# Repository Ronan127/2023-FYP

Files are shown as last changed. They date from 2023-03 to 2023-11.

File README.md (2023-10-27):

# 2023-FYP

Using this repository:

This repository contains the full project folder for my final year project. If you are continuing this project, I recommend cloning this repository or downloading the MATLAB/ and vscode/ folders.

Using the maths model:

The maths model was developed in MATLAB and can be found in MATLAB/v2/.  The Calculations.mlx contains the code I used to produce the plots in the report. The first section loads the stored sets of equations. These equations are produced by the scripts SetCoreEquations.m and SetDesignParameters.m.
To model devices other than the one I used in this project, edit SetDesignParameters.m with your device's parameters and run it.

The next section in Calculations.mlx builds a set of equations from the core equations, the design parameters, the boundary conditions as described in the report, and the position of the device. The equations are fed to mysolver(), and the resulting solution contains T_z, the motor torque required to cause motion.
The solutions are used to create a visualisation of the device, which can be useful to ensure that all the angles lie in the correct quadrants and that the tail is contacting the correct steps. These steps are repeated for each stage of motion.

Next, the model is used to find solutions for a range of positions across a stage of motion. This is how I produced the torque-angle plot in the report. To do this, it first attempts to solve an incomplete set of equations that does not contain the position. The solver will find solutions to what it can, saving time in future steps.
Then, looping through all the positions you want to solve for, the positions are added to the remaining equations and solved. This takes some time, despite making use of parallelization.

Next, the model is used to determine how changing the gear ratios affects the required torque and friction. To do this, it first creates a new set of design parameters that do not define the gear ratio, then the solver loops through different values for the number of teeth on the planet gear. The highest torque and friction required are in Stage 4 and are not at a set angle, so the solver attempts several angles and finds the one that produces the highest torque.
This example can be expanded to explore any design parameter; just make sure to check whether increasing the size of the tail or LIMs changes which steps the LIMS make contact with.

The one major weakness of mysolver() is that it cannot identify whether the equations are overdefined. If you have x == 2 and x == 3, it will just pick the first one, so bear that in mind when using this tool.

Using the converter:

Drake does not support Windows, so Linux or OSX is needed. I set up the conversion pipeline and simulation in Ubuntu using the Windows Subsystem for Linux. I recommend installing Visual Studio code for WSL for these next steps.

This stage primarily uses onshape-to-robot, which can be found at https://github.com/Rhoban/onshape-to-robot
They have a well-documented program, however if you just want to use my scripts, this is what you would need to do:
1. Clone or download vscode/ into your Linux installation
2. Create a Python virtual environment in this folder
3. Run pip install -r requirements.txt
4. Get an Onshape account
5. Get an access key and secret key from https://dev-portal.onshape.com/keys
6. Edit convert.sh with your keys (Note that this is not secure, and there are better ways of doing it. Do not publish this file while it has your keys in it. I have deactivated mine.)
7. Now you need a file to convert. onshape-to-robot has a list of requirements for the onshape file. I recommend you ensure whatever device you build conforms to their guidelines. My design, https://cad.onshape.com/documents/9f7ac96b4bf1f871a2a6bcc9/, can be used as a guideline for naming conventions and subassembly grouping. My code specifically looks for joints named dof_motor_a and dof_motor_b_inv, and links named Tail, Wheel, and Frame.
8. Once you have a device ready, create a new folder containing a file named config.json, with the contents:
   {
    "documentId": "Your document ID",
    "outputFormat": "sdf"
   }
   "Your document ID" is the first set of hex codes in the device's URL. For my design, it is 9f7ac96b4bf1f871a2a6bcc9.
9. Then run "convert.sh yourFolder" where yourFolder is the name of the folder you created in step 8.
10. The folder should now populate with a .sdf file and all of the object files.

Using the simulator:

To run the simulation, run simulation.py. This will open a meshcat instance, which can be opened at http://localhost:7000/. The code here is primarily based on the tutorial: https://deepnote.com/workspace/Drake-0b3b2c53-a7ad-441b-80f8-bf8350752305/project/Tutorials-2b4fc509-aef2-417d-a40d-6071dfed9199/notebook/authoring_multibody_simulat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
simulation.py has many private defines that can be edited, such as the .sdf file location, stair sizes, and motor properties.
If the simulator ever pulls an exception, try decreasing the time step or increasing the no-load speed; it is likely because the feedback from the motor equation is too sharp.

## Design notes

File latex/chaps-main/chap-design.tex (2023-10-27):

\chapter{Design}

In order to validate the model, a device must be designed, built and tested. 

\section{Selection of design parameters}
There are many parameters to consider when designing LIMs, such as gear ratios, lengths, and wheel size. Optimising the design is beyond the scope of this project, but the device does need to work to the extent that it can be used to validate the model. Initially, this project intended to use the early versions of the model to inform the design process. However, as the model was not yet validated, significantly changing key parameters could easily result in a device that is unable to climb stairs at all. Previous projects were able to show inconsistent success. Of the previous projects, Powrie's design was the latest and most informed, and is used as a starting point for this project. Powrie's report specifies the dimensions and gear ratios for the LIMs used in this project.\\

\section{Body design}
The body of the device is the central part that contains the motors and any peripheral devices.
Powrie's design for the body includes a camera, batteries, and extra gearing to increase the torque of his motor. These components are superfluous for the objectives of this project, and are not included in the design. Additionally, the body in Powrie's design protrudes forward significantly beyond the axle of the LIMs. This is done to allow for gearing of the axial motors used in the design, but previous students have found that this protrusion causes the body to collide with the step when climbing, which can result in failure to climb the step. This project uses DC motors with worm gearbox outputs, allowing the motor to be placed at a right angle to the axis. This eliminates the need for significant forward protrusion or additional gearing, and simplifies the construction process. Figures \ref{fig:Powrie-internals} and \ref{fig:internals} shows the body of Powrie's design and this project's design respectively.
\begin{figure}
	\centering
	\begin{subfigure}{.5\textwidth}
		\centering
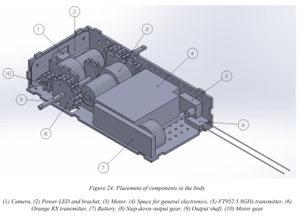
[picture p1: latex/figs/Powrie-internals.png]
		
		\caption{Powrie's design of the body.}
		\label{fig:Powrie-internals}
	\end{subfigure}%
	\begin{subfigure}{.5\textwidth}
		\centering
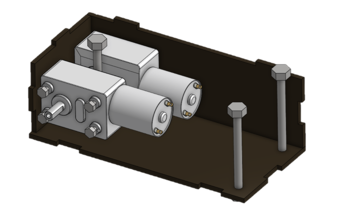
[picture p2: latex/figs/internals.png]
		
		\caption{This project's design of the body.}
		\label{fig:internals}
	\end{subfigure}
	\caption{Body design comparison.}
	\label{fig:bodies}
\end{figure}

\section{Motor selection}
Brushed DC motors often include a gearbox to increase the torque of the output at the cost of speed. For this design, the output shaft must be at a right angle to the motor, which is typically done with a worm gearbox. The most readily available motors that meet these requirements are the JGY-370 12V DC worm gear motors, which come with a range of gear ratios. Initially, the 40 RPM model was selected as it provides similar torque to the EGB-380S with added gearing that Powrie used, however initial tests indicated that additional torque was needed for consistent climbing, so the 6 RPM model was used instead.\\
Additionally, these motors have a self-locking gearbox, which improves the controllability of the device, as shutting off the motors will cause the gearbox to lock and the device to stop moving, rather than allowing the device to fall backwards down the steps.

\section{Control circuits and code}
In order to validate the model, the torque of the motors must be variable and reversible. This project uses a L298n H-bridge controlled by an STM32-F303RE Nucleo board to drive the motors. Two potentiometer sliders are used to control the torque of the two motors independently. The sliders are set up as voltage dividers and connected to the ADC channels of the STM32 microcontroller. The microcontroller sends a direction and PWM signal for each motor to the L298n H-bridge, which controls the motor using PWM. The circuit diagram for this set-up is shown in Figure \ref{fig:circuit-diagram}.

\begin{figure}[!h]
	\centering
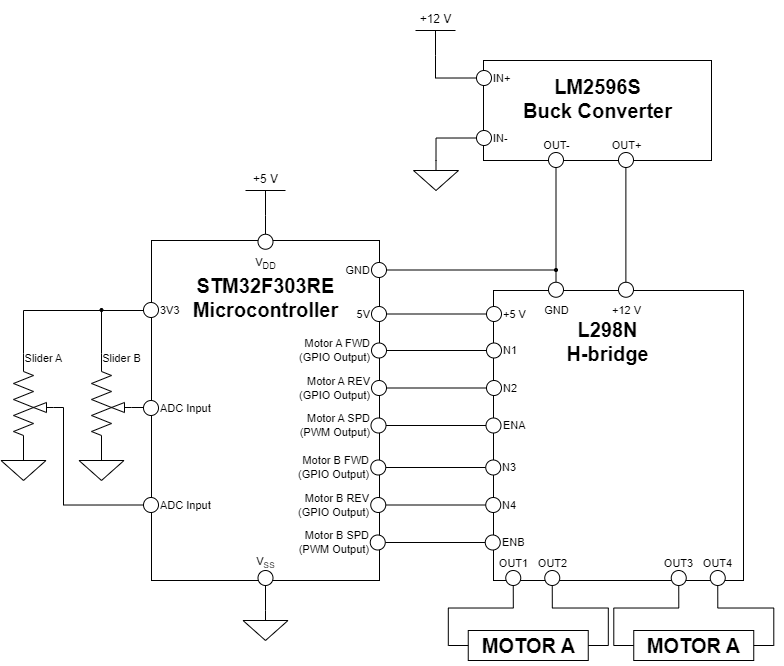
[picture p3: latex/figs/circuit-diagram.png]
	
	\caption{Control system circuit diagram.}
	\label{fig:circuit-diagram}
\end{figure}

The microcontroller is programmed to power off the motors when the sliders are centred, move the motors forward when the sliders are pushed forward, and move the motors in reverse when the sliders are pulled back. The PWM duty cycle is scaled such that when the ADC values are in the centre 20\% of their range, the PWM duty cycle is set to 0\%. When the ADC values are within the top or bottom 5\% of their range, the duty cycle is 100\%. The flow diagram for this code is shown in Figure \ref{fig:controller-flowchart}.

\begin{figure}[!h]
	\centering
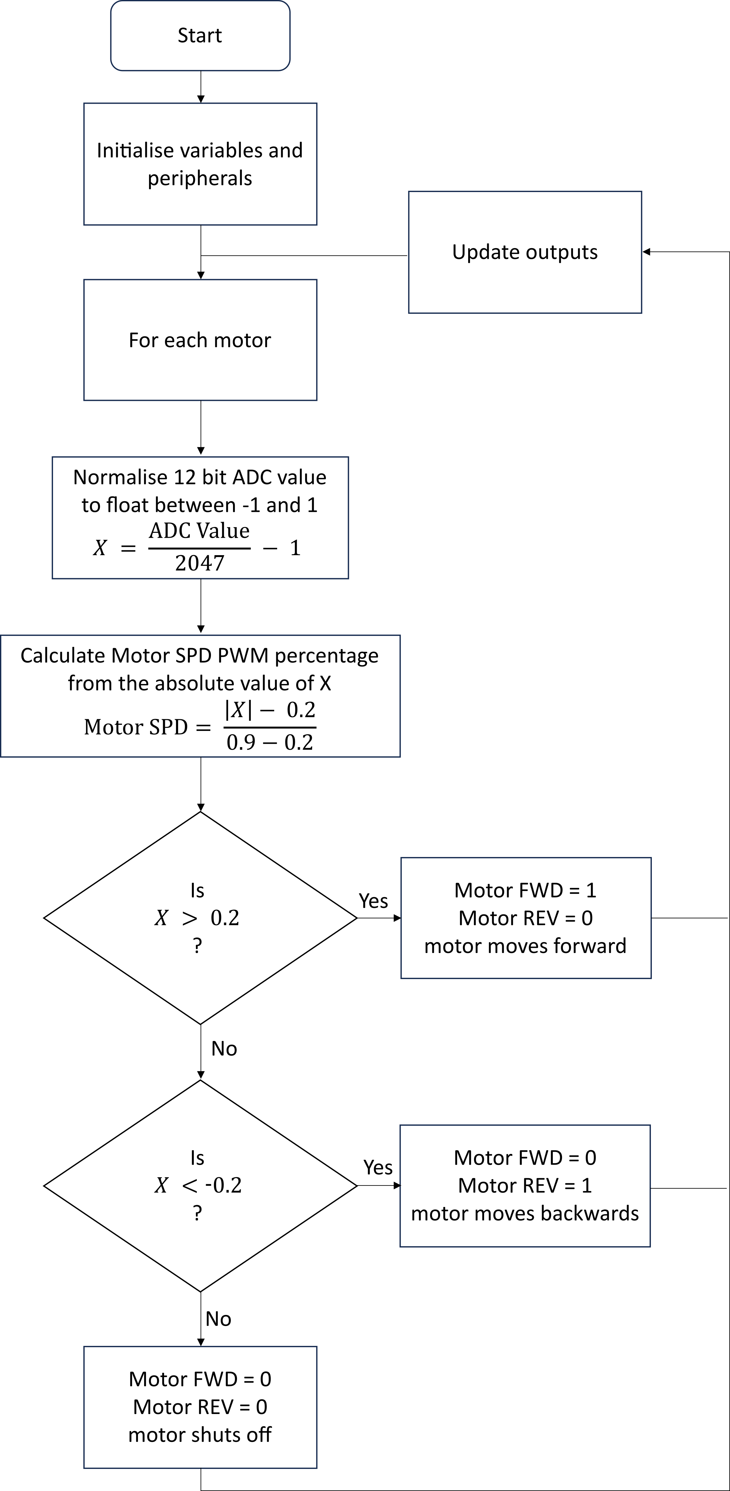
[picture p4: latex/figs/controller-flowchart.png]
	
	\caption{Microcontroller code flowchart.}
	\label{fig:controller-flowchart}
\end{figure}

Initial tests showed that PWM duty cycle is not proportional to torque output on the motors. Instead, even at low duty cycles, the motors can lift a large load, they just do so slowly. This is likely because the self-locking gearbox prevents the axle from ever falling backwards. Consider a DC motor lifting a lever as seen in Figure \ref{fig:lever}. 

\begin{wrapfigure}{r}{0.35\textwidth}
	\centering
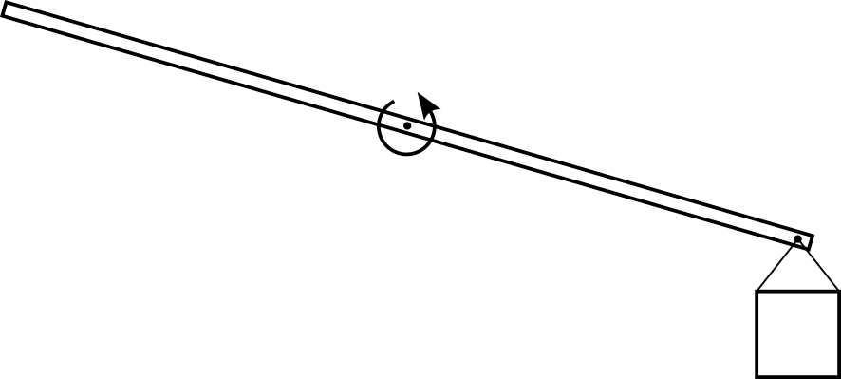
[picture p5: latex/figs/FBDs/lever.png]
	
	\caption{Lever example.}
	\label{fig:lever}
\end{wrapfigure}

Typically, when the PWM signal is on, the motor outputs full torque and moves forward, then when the PWM signal is off the motor outputs no torque and falls backwards. The PWM frequency is typically high enough that the human eye sees this as a smooth motion. However, because of the self-locking gearbox, the axle will lock when the PWM signal is off rather than moving backwards, resulting in an overall forward motion even at low duty cycles. This is quite useful for controlling the motors as the speed of the motors is proportional to the PWM duty cycle regardless of the load it must lift.\\

However, for the validation of the model, the motor torque should be variable and measurable. Brushed DC motor torque is proportional to the current running through it, and the current reduces as the speed of the motor increases. The speed of the motor is also proportional to the terminal voltage. The approximate characteristics of a DC motor are given in Figure \ref{fig:torque-speed}. 
\begin{figure}[!h]
	\centering
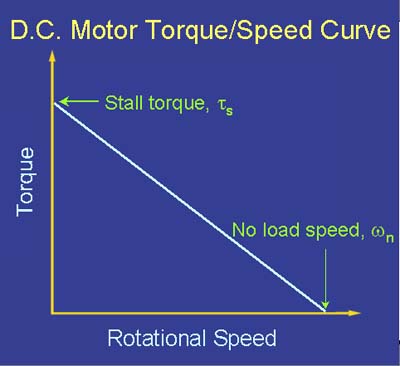
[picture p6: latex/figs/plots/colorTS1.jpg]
	
	\caption{Torque speed plot of a typical DC motor \citep{Page-1999}.}
	\label{fig:torque-speed}
\end{figure}

\noindent The equation describing the torque of a DC motor in relation to motor voltage and speed is then,
\begin{equation}
	T = T_\mathrm{Rated-stall}(\frac{V_\mathrm{Terminal}}{V_\mathrm{Rated}}-\frac{\omega}{\omega_\mathrm{Rated-no-load}})
\end{equation}
where $T$ is the output torque, $T_\mathrm{Rated-stall}$ is the stalling torque at the rated voltage, $V_\mathrm{Terminal}$ is the supply voltage across the motor terminals, $V_\mathrm{Rated}$ is the motor's rated supply voltage, $\omega$ is the rotational speed of the output shaft, and $\omega_\mathrm{Rated-no-load}$ is the speed of the output shaft when no load is placed on it at the rated voltage.\\

\noindent To solve for the stalling torque, $\omega$ is set to $0$. This gives the relation,
\begin{equation}
	T_\mathrm{Stall} = T_\mathrm{Rated-stall}\frac{V_\mathrm{Terminal}}{V_\mathrm{Rated}}
\end{equation}
%??? Move to literature review?
In order to vary the stall torque of the device, the terminal voltage must be varied. For this purpose, an LM2596S buck converter is used to vary the supply voltage.

\section{Construction and testing}\label{sec:construction}

\begin{wrapfigure}{r}{0.35\textwidth}
	\centering
	
	\caption{Built device.}
	\label{fig:device}
\end{wrapfigure}

To build the device, the parts were laser cut from Medium Density Fibreboard (MDF) and Acrylic. The outer surface of wheels is coated with Patex, a rubbery adhesive which is left to dry, increasing the grip of the wheels. The assembly is relatively straightforward, however it was found that the laser cut gears did not mesh well, causing them to get stuck. To address this, the teeth of the gears were filed down until they could mesh easily. This has the disadvantage of increasing kickback on the gears. However, this has little impact on performance as for all stages of motion, the gears are engaged in one direction only. The device is shown in Figure \ref{fig:device}.\\

Initial tests show that the device is capable of climbing up two steps sequentially, which is more than any previous project achieved. This relative success can be attributed to the shorter forward protrusion of the body and possibly a higher grip on the surface of the wheels. However, the device struggled to climb a third step, this is because climbing the third step involves Stage 4 motion, which requires significantly higher torque than the previous stages. To address this, the body of the device was rebuilt using a JGY-370 gearbox motor which is geared for a higher torque. \\
After this change, the device was able to consistently climb many sequential steps, and the lower speed due to the higher gear ratio made the device easier to control during the climbing motion. Figure \ref{fig:device-climbing} shows the device climbing a flight of stairs. Initial tests also show that by applying a forward torque to one LIM and a reverse torque to the other, the device is capable of turning on the spot. However this motion is inconsistent as the LIMs can start to lift, at which point the turning stops.
\begin{figure}[!ht]
	\centering
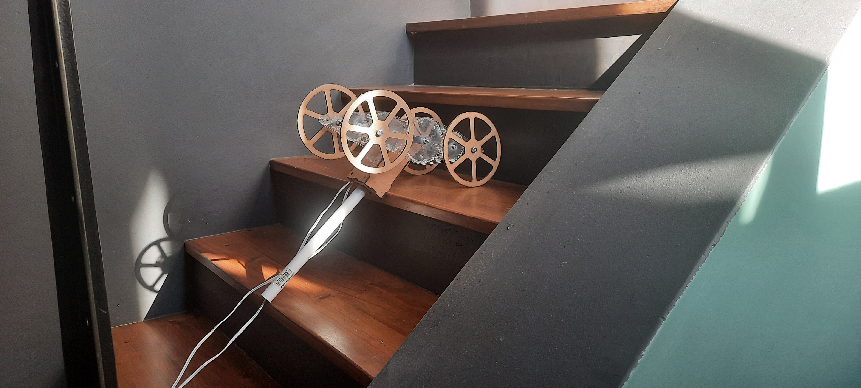
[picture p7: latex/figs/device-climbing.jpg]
	
	\caption{Device climbing stairs.}
	\label{fig:device-climbing}
\end{figure}
%When the motor is turning it also acts as a generator, and produces a voltage known as back emf which is proportional to the speed of the motor. 
%\begin{equation}
%	E_b \propto \omega
%\end{equation}
%Where $E_b$ is the back emf and $\omega$ is the speed of the motor.
%
%The approximate circuit diagram of a DC motor is shown in figure ???. The current running through the motor is proportional to the difference between the supply voltage and the back emf.
%\begin{subequations}
%	\begin{align}
%	I &= \frac{V-E_b}{R_a
%	I &\propto V-E_b
%	\end{align}
%\end{subequations}

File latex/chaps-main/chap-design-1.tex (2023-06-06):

\chapter{Design- 1st iteration}

Starting with Powrie's device as it is the most developed of the previous projects.\\
Attempted to use mathematical model to identify potential improvements, however I struggled to get objective improvements, increasing one parameter often may improve the ability to flip but hinder the ability to climb overall, and removing material should only be done if it has minimal effect on structure strength, something that would take much time to determine (possibly with FEM?). Such optimisations are beyond the scope of the project, I'm not trying to create a perfectly optimised device, I'm trying to create a working device so I can describe its function. Powrie’s device is working to some extent, so the first design iteration should deviate minimally from his design.\\
Powrie's design for the LIMs is copied as accurately as possible, could possibly even use his laser cutting templates to manufacture. Fortunately he provides a detailed builder's guide, allowing me to design and build ASAP so I can focus on the math model. The robot body is changed significantly. Powrie uses external gears on an already geared motor, this is unnecessary, as geared motors come in a variety of ratios. I use a JGY-370 motor, as I believe the worm gearbox is well suited to this purpose, it allows me to make a thinner body that doesn't protrude as far forward beyond the axle. The tail is designed based on Powrie’s concepts. The motors selected produce more torque than the ones Powrie selected, even with his additional gearing, so they should be up to the task. Later iterations could combine the worm gearbox with even more powerful brushless motors.

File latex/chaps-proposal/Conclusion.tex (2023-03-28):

\chapter{Conclusions}
%In conclusion, sound localisation is a promising technology that could be used in more applications if it were more precise. The proposed project will design and build a sound localisation device, and investigate methods to improve its performance. The project activities have been outlined and planned, risks have been assessed, and an expected budget of R221725 is presented.
USAR robots are a promising technology for disaster response. Reducing the cost of these robots will make them more accessible. The proposed project will provide a model to describe the kinematics of USAR robots that use LIMs for locomotion to reduce costs, and will produce a prototype of a USAR robot platform to show that the model is accurate. The result of these activities will be a validated model that can be used to inform future USAR designs using LIMs.\\

\noindent The project activities have been outlined and the project risks have been assessed and mitigated. The expected duration of the project is 8 months and the expected budget is R265 400.

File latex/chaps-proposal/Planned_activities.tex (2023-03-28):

\chapter{Planned Activities}

\section{Review Literature}
Study work by previous students on LIMed robots. Additionally, research existing solutions for USAR platforms and identify methods that are applicable to this project. 

\section{2D Simulation}
Perform a simple 2D simulation of a LIMed robot platform to gain a greater understanding of how it functions.

\section{Create Model}
Create a mathematical model to describe the kinematics of a LIMed robot platform. This will be presented in a way that describes how the degrees of freedom will move as a function of the platform's state and the torque applied to it.

\section{Compile Design Requirements}
Determine the requirements for the system, including functions that the platform must be able to perform and the cost of the platform. List these requirements in a way that they can be used to evaluate different concepts.

\section{Design Platform}
Compare concepts for a LIMed robot platform, then select the preferred concept based on its ability to meet the design requirements. Then create a detailed design of the robot platform.

\section{Simulate Platform}
Perform a mature simulation of the designed platform to ensure it will meet the requirements.

\section{Produce Prototype}
Construct a prototype of the robot platform. This will involve a combination of manufacture by the MMW, and assembly of the components.

\section{Validate Model}
Test that the model accurately describes the kinematics of a LIMed system through experimentation using the prototype.

\section{Finalise Report}
Document the entire project, including the process of creating a model, designing and production of the prototype, and experimentation. Comment on whether the model can be used to accurately describe the LIM system.\\\\

\noindent Please see Appendix A for the budget and time allocation of these activities.

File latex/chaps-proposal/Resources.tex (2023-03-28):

\chapter{Resource use and end of life strategy}

This project will build a prototype device that has a motor, a controller, wheels, and several custom parts such as gears and frames. A battery is unlikely to be included as it may be too expensive for a prototype build which can otherwise be wired to a power supply.
The prototype will likely benefit from having a low mass, so there is already an incentive to use materials sparingly. Before construction, the design will be simulated to ensure that it meets requirements; this will mitigate the chance that a second prototype will need to be built. Upon completion of the project, the prototype will be disassembled and the motor, controller, and wheels can be reused in future projects. The custom parts are specific to this design so will not be suitable for most reuse applications; they shall be recycled. If the materials are such that they cannot be recycled, then they shall be disposed of instead. These materials will be chemically inert (not hazardous).

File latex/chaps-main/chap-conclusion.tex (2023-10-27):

\chapter{Conclusions}

This report details the design, modelling, and model validation of a novel gearing system for robot locomotion. The advantage of this LIM gearing system is that it allows a device to roll forward or climb steps using a single actuator, reducing costs, while also being able to fit into low voids. The model produced by this report could be used to inform the design of future USAR robots. This project builds and improves upon previous work, and produces the first LIM robot capable of climbing steps consistently and sequentially. \\

To explore the motion of the LIMs, a preliminary two-dimensional simulation was performed, and the stair climbing motion of the device was categorised into six distinct stages. This project proposes a mathematical model to describe the motion a LIMed device, using the MATLAB symbolic toolbox. The maths model consists of a large set of simultaneous equations that are solved simultaneously, and this report presents an algorithm that uses the MATLAB functions to efficiently solve this large set of equations. Additionally, this project explores the use of Drake, a multi-body simulator, to model the device. \\

Both the maths model and simulation are validated against real world data. The validation showed that the torque required to climb stairs sequentially was 16.4\% higher than the maths model predicted, and 5.9\% higher than the simulation predicted. This report explores the reasons for this error, which are attributed to imperfect assumptions and calibration methods.\\

In conclusion, this project was successful in completing its objectives. Both the model and simulation have been validated and their error has been quantified, they can be used to inform future work on LIMed robots.

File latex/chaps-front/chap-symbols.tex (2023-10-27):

\chapter{List of symbols}
% Use stb-nomenclature + siunitx

\begin{Nomencl}[1cm]
\NomGroup{Constants}%-----------------------------------------------
    \item[$g = $] \qty{9.81}{m/s^2}
\NomGroup{Components}%-----------------------------------------------
	\item[1] LIM frame
	\item[2] Central or "sun" gear
	\item[3] Front idler gear
	\item[4] Rear idler gear
	\item[5] Front outer or "planet" gear
	\item[6] Rear outer or "planet" gear
	\item[7] Body of the device, including the motors and the tail
\NomGroup{Variables}%-----------------------------------------------
	\item[$I_n$]
	\UnitLine{Mass moment of inertia of component n, normal and relative to its relevant axis}{kg.m^2}
	\item[$M_{\mathrm{React}n}$]
	\UnitLine{Reaction moment that the ground or step exerts on wheel n}{N.m}
	\item[$m_n$]
	\UnitLine{Mass of component n}{kg}
	\item[$N$]
	\UnitLine{Number of the step on which the front wheel is placed}{~}
	\item[$N_2$]
	\UnitLine{Number of the step on which the tail makes contact}{~}
	\item[$N_{\mathrm{Planet}}$]
	\UnitLine{Number of teeth on the outer gear}{~}
	\item[$N_{\mathrm{Sun}}$]
	\UnitLine{Number of teeth on the central gear}{~}
	\item[$r_n$]
	\UnitLine{Radius of gear n}{rad/s^2}
	\item[$r_w$]
	\UnitLine{Radius of the wheels}{m}
	\item[$s_{7\mathrm{end}y}$]
	\UnitLine{3x1 Position vector of component the end of the tail}{m}
	\item[$T$]
	\UnitLine{Torque exerted by the motor of component 7 on component 2}{N.m}
	\item[$T_\mathrm{Rated-stall}$ ]
	\UnitLine{The motor stalling torque when the rated voltage is applied}{N.m}
	\item[$t$]
	\UnitLine{Time}{s}
	\item[$V_\mathrm{Rated}$ ]
	\UnitLine{The rated motor voltage}{V}
	\item[$V_\mathrm{Terminal}$ ]
	\UnitLine{The voltage across the motor terminals}{V}
	\item[$\theta_n$]
	\UnitLine{Clockwise angle of component n}{rad}
	\item[$\dot{\theta}_{\mathrm{Frame}}$]
	\UnitLine{Angular velocity of the frame}{rad/s}
	\item[$\dot{\theta}_{\mathrm{Planet}}$]         
	\UnitLine{Angular velocity of the outer gear and wheel}{rad/s}
	\item[$\dot{\theta}_{\mathrm{Sun}}$]
	\UnitLine{Angular velocity of the central gear}{rad/s}
	\item[$\dot{\theta_n}$]
	\UnitLine{Clockwise angular velocity of component n}{rad/s}
	\item[$\ddot{\theta_n}$]
	\UnitLine{Clockwise angular acceleration of component n}{rad/s^2}
	\item[$\mu_5$]
	\UnitLine{Static coefficient of friction between the front wheel and the surface it makes contact with}{~}
	\item[$\mu_{\mathrm{tail}}$]
	\UnitLine{Static coefficient of friction between the tail and the surface it makes contact with}{~}
	\item[$\omega$ ]
	\UnitLine{Motor shaft angular velocity}{rad/s}
	\item[$\omega_\mathrm{Rated-no-load}$ ]
	\UnitLine{Motor shaft angular velocity when the rated voltage is applied and the motor is unloaded}{rad/s}
	\item[$\vec{a_n}$]
	\UnitLine{3x1 Acceleration vector of component n}{m/s^2}
	\item[$\vec{F}_{\mathrm{React}n}$]
	\UnitLine{3x1 Force vector the ground or stairs exert on component n}{N}
	\item[$\vec{f_n}$]
	\UnitLine{3x1 Force vector that component n exerts on component 1}{N}
    \item[$\vec{\mathrm{gf}_3}$]
	\UnitLine{3x1 Force vector that gear n exerts on the inner gear that it contacts}{N}
	\item[$\vec{l_n}$]
	\UnitLine{3x1 Displacement vector from the motor axis to component n}{m}
	\item[$\vec{s_n}$]
	\UnitLine{3x1 Position vector of component n}{m}
	\item[$\vec{u}$]
	\UnitLine{3x1 Displacement vector from the motor axis to the point where the tail contacts the step}{m}
	\item[$\vec{v_n}$]
	\UnitLine{3x1 Velocity vector of component n}{m/s}
	\item[$\vec{w_n}$]
	\UnitLine{3x1 Force vector resulting from the weight of component n}{N}
\NomGroup{Subscripts}%----------------------------------------------
    \item[$x$] Component of a Cartesian vector in the x direction
    \item[$y$] Component of a Cartesian vector in the y direction
    \item[$z$] Component of a Cartesian vector in the z direction
\end{Nomencl}
\clearpage
\begin{Nomencl}[1cm]
\NomGroup{Abbreviations}%-----------------------------------------------
\item[DC] Direct Current
\item[FR] Functional Requirement
\item[LIM] Load Intuitive Module
\item[MATLAB] Matrix Laboratory
\item[MDF] Medium Density Fibreboard
\item[PR] Performance Requirement
\item[PWM] Pulse Width Modulation
\item[RPM] Rotations Per Minute
\item[SR] Stakeholder Requirement
\item[UCT] University of Cape Town
\item[USAR] Urban Search And Rescue
\item[WSL] Windows Subsystem for Linux
\end{Nomencl}

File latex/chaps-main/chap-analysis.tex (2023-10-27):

\chapter{Analysis}

The objective of this analysis is to validate the model and the simulation. The values calculated in the maths model and simulated in Drake are compared with the experimental data to determine the validity of the maths model and the simulation.

\section{Qualitative comparison}

The motor torque over time for Stage 1 motion was recorded during the Drake simulation, and is shown in Figure \ref{fig:torque-stage-1}. This shows a similar curve to the plot of recorded current, which is shown again in Figure \ref{fig:current-2}. The simulation completed Stage 1 in 2.8 s, which is faster than the real device which took 3.25 s. The noise in the simulated data is due to oscillations caused by Equation \ref{eq:torqueVoltageSpeed}, which acts as a proportional feedback controller on the speed in the simulation. This oscillation could be reduced by decreasing the simulation time step, however this would proportionally increase the simulation time taken, and a low time step of 0.01 ms is already selected. Both plots show a large spike as the motors are powered on and a slight dip before Stage 1 completes. This indicates that the torque produced by the device throughout the simulation accurately matches the torque that the real device would produce.
\begin{figure}[!ht]
	\centering
	\begin{subfigure}{.5\textwidth}
		\centering
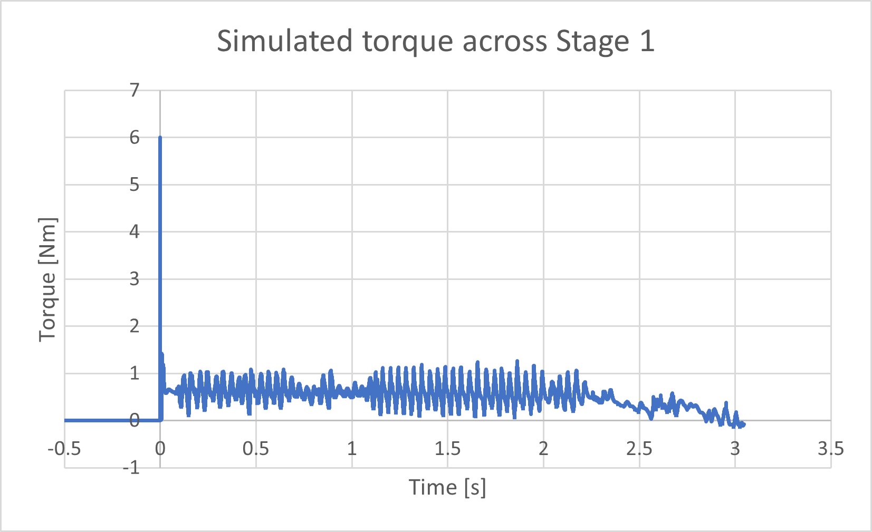
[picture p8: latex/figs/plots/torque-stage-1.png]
		
		\caption{Torque recorded over time as the \\simulated device completes Stage 1.}
		\label{fig:torque-stage-1}
	\end{subfigure}%
	\begin{subfigure}{.5\textwidth}
		\centering
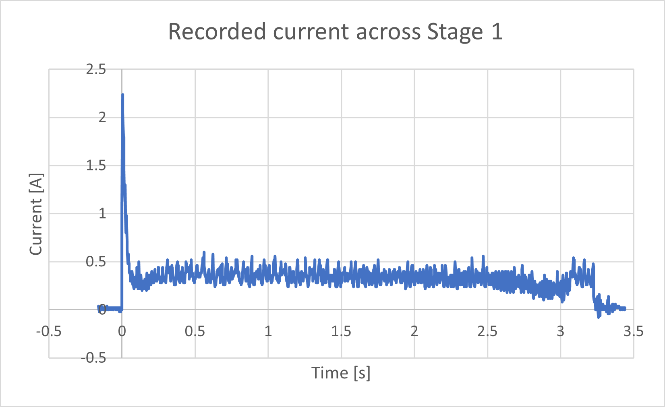
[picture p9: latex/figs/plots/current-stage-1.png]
		
		\caption{Current recorded over time as the device completes Stage 1.}
		\label{fig:current-2}
	\end{subfigure}
	\caption{Simulated current and recorded torque.}
	\label{fig:torque-current}
\end{figure}

\section{Quantitative comparison}

The torque measurement experiment gives two values for each stage of motion, the torque required to cause some partial movement, and the torque required to cause full movement. These values will be referred to as $T_\mathrm{Partial}$ and $T_\mathrm{Full}$ respectively, and are shown in Figure \ref{fig:torque-experiment}.

\begin{figure}[!h]
	\centering
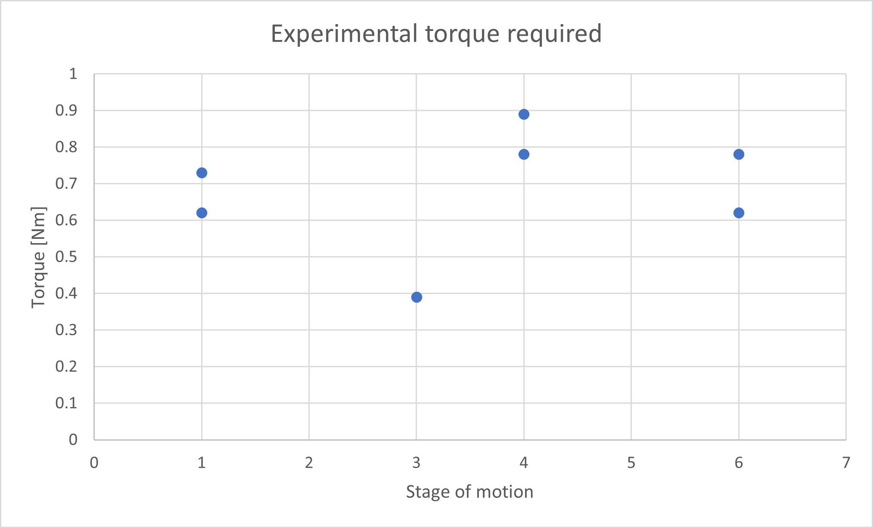
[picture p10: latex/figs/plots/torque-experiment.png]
	
	\caption{Required torques for each stage determined experimentally}
	\label{fig:torque-experiment}
\end{figure}

In Figure \ref{fig:torque-experiment}, there are two points for each stage, the higher of which is $T_\mathrm{Full}$ and the lower is $T_\mathrm{Partial}$. In cases where only a single point is present, there was no torque that would cause a partial movement; meaning that if the torque is high enough to start the movement, it is also high enough to complete the movement. Stages 0, 2, and 5 are omitted as the device does not push against gravity in these stages, so the torque required is negligible.\\

To determine the required torque in the simulation, the torque measurement experiment is simulated. The torque required across each stage of motion has already been calculated using the maths model, as shown in Figure \ref{fig:bigplot}. The required torque at the start of each stage is equivalent to $T_\mathrm{Partial}$, as this is the torque that will cause the motion to start. The highest required torque for each stage is $T_\mathrm{Full}$, because if the device can output this torque it will be able to complete the full stage of motion. The required torque produced by the simulation and the maths model are shown side by side with the experimental data in Figure \ref{fig:torque-comparison}.\\

\begin{figure}[!h]
	\centering
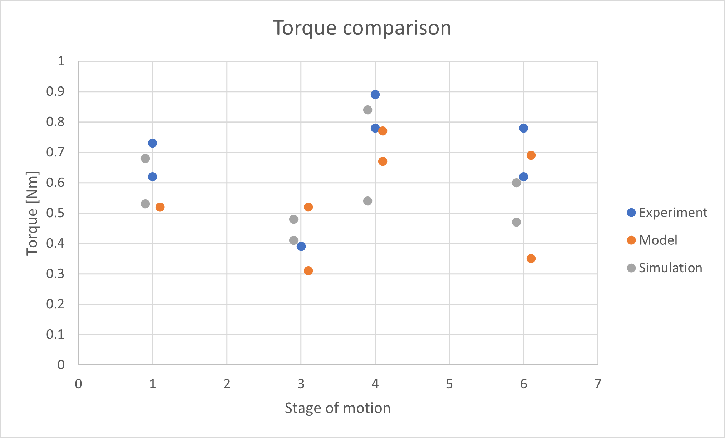
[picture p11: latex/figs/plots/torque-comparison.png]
	
	\caption{Required torques for each stage from different sources.}
	\label{fig:torque-comparison}
\end{figure}

Figure \ref{fig:torque-comparison} shows that the model, simulation, and experiment all show similar trends but produce different values. In Stages 1, 4, and 6, the model and simulation both produce a lower required torque than the device actually needs. In Stage 3, the device needs less torque to complete the motion than the model and simulation predict.\\
To test the accuracy of the model and simulation across a range of design parameters, the experiment and comparison were repeated twice, once with a 60 cm long tail in place of the 30 cm one, and once with a 340 g mass attached to the body of the device. The comparison between these results are shown in Figures \ref{fig:torque-comparison-tail} and \ref{fig:torque-comparison-mass}. These plots show similar trends, indicating that the model and simulation give consistent results for a range of design parameters.

\begin{figure}
	\centering
	\begin{subfigure}{.5\textwidth}
		\centering
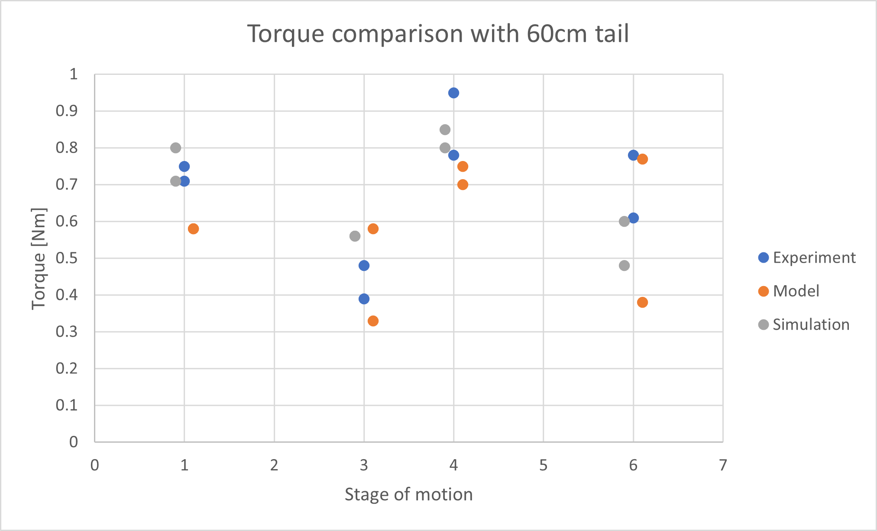
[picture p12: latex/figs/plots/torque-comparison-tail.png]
		
		\caption{Required torques for each stage when \\device has a 60 cm tail.}
		\label{fig:torque-comparison-tail}
	\end{subfigure}%
	\begin{subfigure}{.5\textwidth}
		\centering
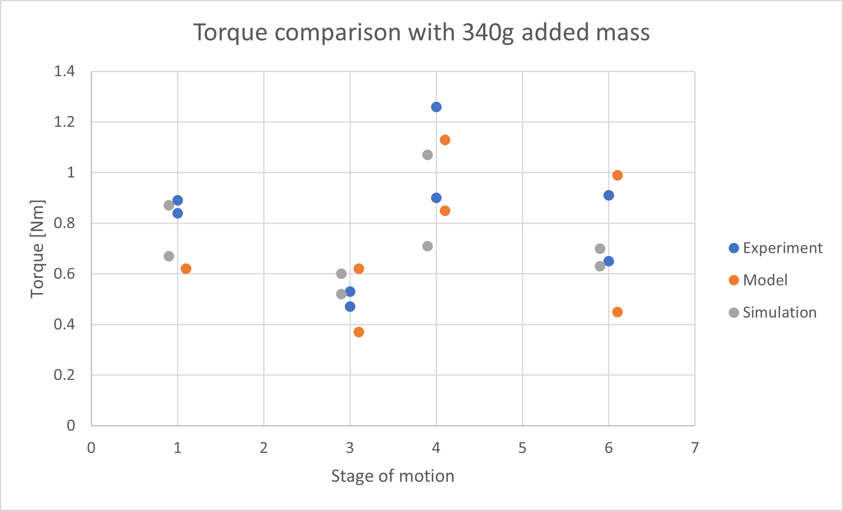
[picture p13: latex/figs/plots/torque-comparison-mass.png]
		
		\caption{Required torques for each stage when \\device has an added 340 g mass.}
		\label{fig:torque-comparison-mass}
	\end{subfigure}
	\caption{Required torques for each stage from different sources, with varied design parameters.}
	\label{fig:torque-comparison-tailMass}
\end{figure}

\section{Assessment of error}

Table \ref{tab:error} shows the percentage error of the required torque produced by the model and simulation for the original device. Negative error indicates that the model or simulation produced a lower torque value than the experiment required. The simulation is shown to be more accurate than the maths model for most data points.\\

\begin{table}[!ht]
	\centering
	\caption{Percentage error of required torque for each stage of motion in the model and simulation.}
	\label{tab:error}
	\begin{tabular}{|l|l|l|l|l|l|l|l|l|}
		\hline
		~ & Stage 1 & ~ & Stage 3 & ~ & Stage 4 & ~ & Stage 6 & ~ \\ \hline
		~ & Partial & Full & Partial & Full & Partial & Full & Partial & Full \\ \hline
		Model & -16.1\% & -28.8\% & -20.5\% & 33.3\% & -14.1\% & -13.5\% & -43.5\% & -11.5\% \\ \hline
		Simulation & -14.5\% & -6.8\% & 5.1\% & 23.1\% & -30.8\% & -5.6\% & -24.2\% & -24.4\% \\ \hline
	\end{tabular}
\end{table}

The full torque required to complete Stage 4 motion is the most important to design around, as this is shown to be the highest torque the device will need. In this stage, the maths model has an error of -14.1\% and the simulation has an error of -5.6\%, which indicates that one should design for at least 16.4\% higher torque than the models suggest. However, other stages of motion show errors of up to 43.5\%, which is very high and indicates that there may be some incorrect assumptions in the models.\\

Identifying the source of the error is not essential for the purposes of informing design, one can simply design the motors to have at least 2 times the calculated required torque. However, analysing the source of this error is important in order to improve future versions of the model.\\

\begin{wrapfigure}{r}{0.35\textwidth}
	\centering
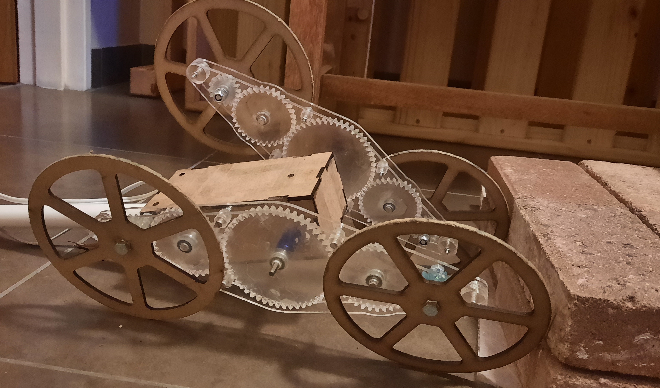
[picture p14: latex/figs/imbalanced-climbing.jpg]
	
	\caption{Device failing to climb as one LIM lifts ahead of the other}
	\label{fig:imbalanced-climbing}
\end{wrapfigure}

In Stage 1, the model predicts that there is no torque that will cause partial movement. As the device lifts the torque required decreases, so if the torque is high enough to start lifting, it is high enough to complete Stage 1 motion. However, Figure \ref{fig:torque-comparison} shows that there is a range of torques that produce partial motion in the experimental and simulated data. The most likely cause for this is that some assumption made in the maths model is invalid. Although the calculations are done differently, the simulation is subject to the same rigid body and friction assumptions as the maths model. The main discrepancy between the two is that the simulation allows motion in three dimensions while the model is limited to two. As there is a large difference between the results of the model and the simulation, it is likely that the three-dimensional movement is what allows the device to get stuck part way during Stage 1. Initial tests showed that if one of the LIMs moves ahead of the other, the device will tip slightly, putting more weight on the LIM that falls behind, preventing the LIM from lifting unless it has excessive torque. An example of this is shown in Figure \ref{fig:imbalanced-climbing}. It is likely that even when the LIMs appear to move in unison, a slight imbalance can cause the motion to stop part way when the motor torque is close to the required torque. To address this error, one could update the maths model to allow movement in three dimensions, however this would drastically increase the complexity and the calculation time of the model, and is excessive when tools for three-dimensional simulation such as Drake are readily available.\\
\clearpage
\begin{wrapfigure}{r}{0.35\textwidth}
	\centering
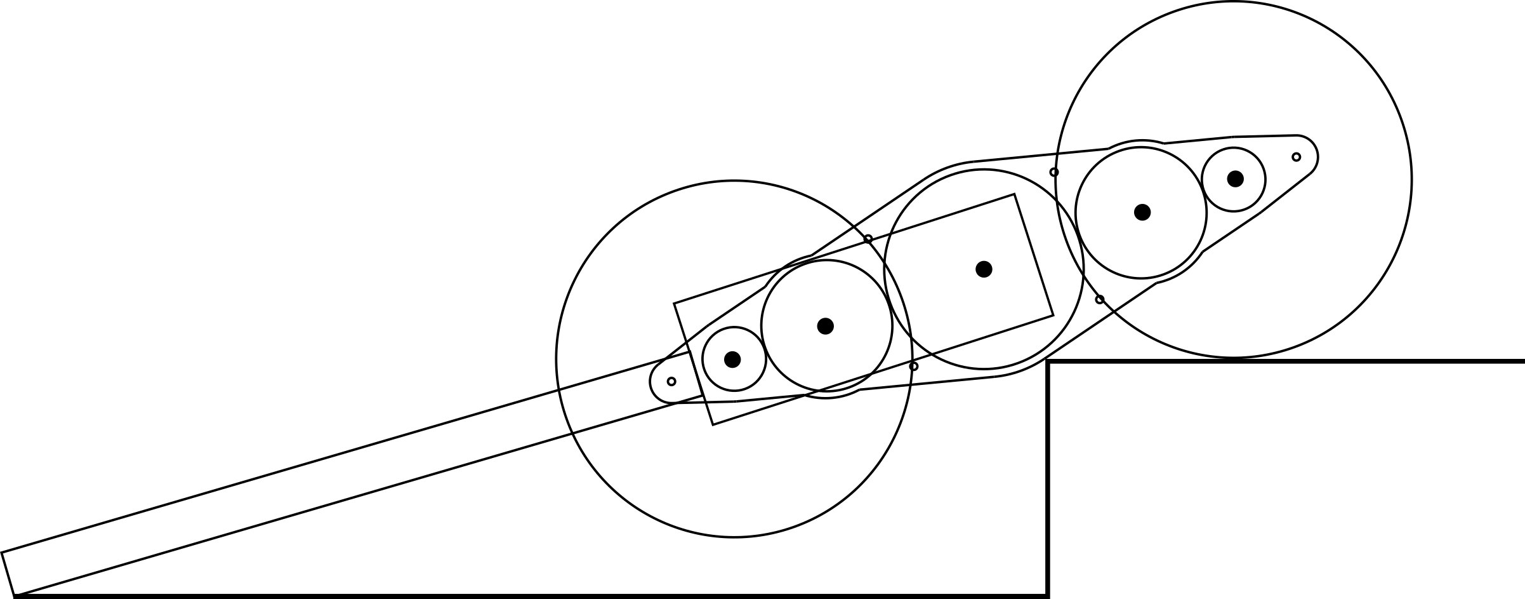
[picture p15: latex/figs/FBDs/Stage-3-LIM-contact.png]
	
	\caption{Frame of the LIM making contact with the edge of the step in Stage 3}
	\label{fig:Stage-3-LIM-contact}
\end{wrapfigure}
In Stage 3, the experiment shows that there is no torque that causes partial motion. However, the simulation indicates that there is a small range of torques that cause partial motion, and the maths model indicates that there is a large range of torques that cause partial motion. Both the simulation and the maths model also indicate that the required torque is higher than the experimental value. The reason for this error in the maths model is likely because it incorrectly assumes that the frame of the LIM will not come into contact with the step. When the device climbs in Stage 3, the frame of the LIM slides along the edge of the step while the front wheel pulls the device up the step, which is illustrated in Figure \ref{fig:Stage-3-LIM-contact}.
The step supports the frame of the LIM, so that the device needs less torque in order to overcome gravity, which explains why the actual device needs less torque to complete the stage of motion than the model predicted. Interestingly, the frame does not typically make contact with the step in Stage 6 because the backwards force from the tail on the step makes the LIMs favour lifting the rear wheel instead of rolling forward. To address this error, the model could be updated to model the contact between the step and the LIM frame, however this would be difficult to do analytically as the LIM frame has an irregular shape. \\
The simulation does model the contact between the LIM frame and the step, however it still indicates that there should be partial movement and that the required torque is higher than the experimental value. Initially it was though that this was because the coefficient of friction between the LIM frame and the step is higher in the simulation than in reality, as it defaults to 1.0. However, inspection of the simulation revealed that in Stage 3 the front wheel simply does not roll forward when the motor torque is low. The LIMs will rotate, lifting the back wheel, but the front wheel does not rotate forward so the frame of the LIM is never supported by the step. This may be because the teeth of the simulated gears do not mesh well and become stuck when the torque is not high enough. As stated in Section \ref{sec:construction}, the real gears had to be filed down in order to mesh well. This indicates that there may be a flaw in the design of the gears.\\

Another potential source of error comes from the calibration of the motors. The voltage torque calibration experiment in Section \ref{sec:Voltage-torque calibration} was used to produce Equation \ref{eqTorqueVoltage}, which was later used to calculate the experimental required torque from the measured voltage. An error in the calibration method could cause all of the experimental results to be off by a constant factor. The method of this experiment involved using the motors to lift a weight with a lever. Typically in this style of experiment, the motor torque would reach an equilibrium with the moment from the weight and the lever would stop moving. However, as the gearbox on the motors is self-locking, the lever cannot move in reverse. This means that if the lever ever lifts beyond the equilibrium point, it will not fall back to the equilibrium point and the recorded lever angle will be higher than the motors could actually output. There are two possible ways that the lever can lift beyond the equilibrium point in this experiment. Firstly, if the lever and the mass have a significant momentum when they reach the equilibrium point, they will move beyond it; this is mitigated by the high gear ratio on the motor which causes it to move quite slowly. Secondly, as the mass is attached to the lever by string, it can act as a pendulum. The swing of the pendulum will sometimes make it easier for the lever to lift, and sometimes make it harder. This combines with the self-locking gearbox to cause the lever to inch forward while the pendulum is helping it, then the gearbox locks when the pendulum swings the other way. This is visualised in Figure \ref{fig:lever-swinging}. The net result is that the lever moves slightly beyond the equilibrium point. \\

\begin{figure}[!h]
	\centering
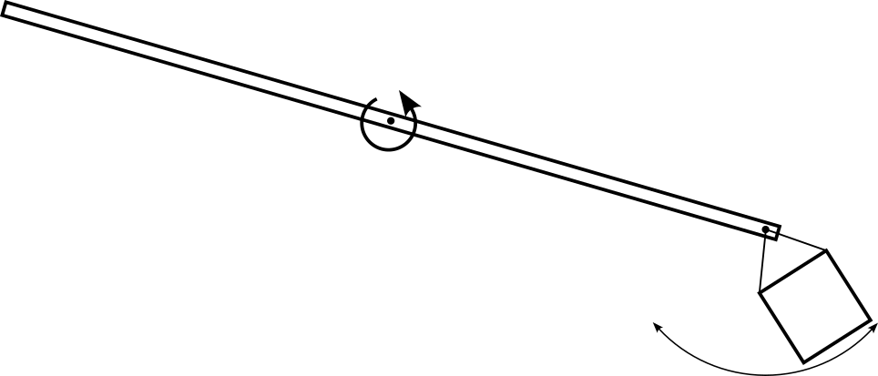
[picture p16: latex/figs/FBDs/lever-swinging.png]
	
	\caption{Visualisation of the mass acting as a pendulum on the end of the lever.}
	\label{fig:lever-swinging}
\end{figure}

If the motors are imperfectly calibrated and appear to produce more torque than they actually do, it would help explain why the experimental torques are higher than the modelled and simulated torques in Stages 1, 3 and 6. This error could be reduced by attaching the mass directly to the lever rather than by string ,however there will always be some degree of error when comparing a theoretical model to the real world.

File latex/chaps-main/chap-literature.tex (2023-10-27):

 \chapter{Literature review}

\section{USAR robots}

\begin{wrapfigure}{r}{0.35\textwidth} %this figure will be at the right
	\centering
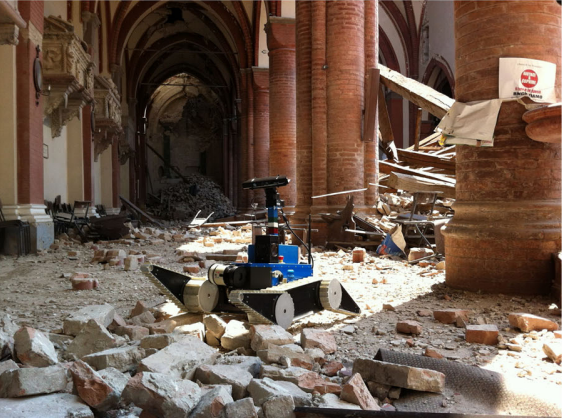
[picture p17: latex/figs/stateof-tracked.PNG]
	
	\caption{A tracked USAR robot, with paddles for obstacle climbing \citep{stateof}.}
	\label{stateof tracked}
\end{wrapfigure}

In both natural and man-made disasters, USAR operations are critical for reducing casualties. Robots can be deployed in USAR operations to complement human and canine rescuers. Robots have the advantage of being able to be deployed in scenarios too small or too dangerous for humans, and aerial robots such as quadcopters are extremely effective at quickly mapping terrain and providing situational awareness to teams. Other emerging applications of USAR robotics are remote fire fighting, victim interaction, and extraction \citep{stateof}.\\
\begin{wrapfigure}{l}{0.35\textwidth} %this figure will be at the left
	\centering
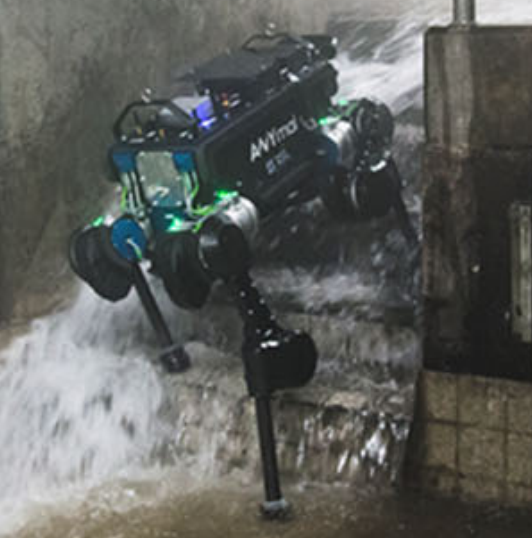
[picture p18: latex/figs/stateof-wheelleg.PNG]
	
	\caption{ANYmal, a legged USAR robot \citep{stateof}.}
	\label{stateof wheelleg}
\end{wrapfigure}

In order to perform USAR operations, robots need some form of locomotion. For ground robots, this typically involves either tracks, wheels, or legs. \citep{stateof}. Tracked robots with actuated paddles for obstacle climbing, such as the one shown in Figure \ref{stateof tracked}, have been found to perform extremely well. This is evident by their representation in the winners of the Robocup Rescue Robot League (RRL), an event in which teams compete to produce robots for versatile USAR operations \citep{Sheh-2016}. Wheeled robots are generally the simplest and easiest to repair, but can get stuck more easily in uneven terrain. Legged robots provide the advantage of not needing a continuous path, and rapid developments in optical sensors and control systems are enabling them to be even more viable. Wheel-leg hybrid systems will use legged motion for navigating difficult terrain, and wheels when on smooth ground \citep{stateof}. 
\newpage
\section{Load-Intuitive Modules} %~~~~~~~~~~~~~~~~~~~~~~~~~~~~~~~~~~~~~~~~~~~~~~~~~~~~~~~~~~~~~~

\begin{wrapfigure}{r}{0.35\textwidth} %this figure will be at the right
	\centering
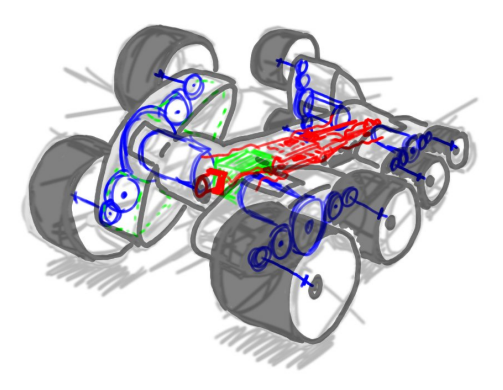
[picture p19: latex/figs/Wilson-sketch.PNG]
	
	\caption{Systems layout of Wilson's LIM device \citep{Wilson-2013}.}
	\label{Wilson sketch-lit}
\end{wrapfigure}

A Load-Intuitive Module (LIM) refers to a wheel system proposed by Matthew Wilson, shown in Figure \ref{Wilson sketch-lit} \citep{Wilson-2013}. The LIM system uses a two outer "minor wheels" placed on a central hub that can be rotated as a "major wheel". The minor wheels are geared to the central hub such that they drive the vehicle, however if they experience high resistance, for example from hitting an obstacle, the torque will cause the major wheel to rotate instead, flipping one of the minor wheels over the obstacle to automatically climb it. The system is referred to as "Load-Intuitive" because it will intuitively climb over obstacles in response to increased load on the wheels. LIMs are designed to be used in low cost USAR robots, allowing them to climb over objects without the need for many actuators.\\

One advantage LIMs provide over existing locomotion methods is that they can climb obstacles higher than their profile, meaning they can enter low voids while rolling, and climb relatively tall obstacles by flipping over them. Another advantage is that LIMs require minimal actuation, one motor can be used to drive both the rolling and flipping motion, which will reduce costs when compared with other designs.\\

\noindent "LIMed" robot platforms (platforms using LIMs for locomotion) were built individually by four final year students at UCT \citep{Wilson-2013}, \citep{Haskel-2017}, \citep{Buchanan-2018}, and \citep{Powrie-2019}. These platforms show some success in climbing a single step, albeit inconsistently.

\subsection{Wilson's LIM robot} %~~~~~~~~~~~~~~~~~~~~~~~~~~~~~~~~~~~~~~~~~~~~~~~~~~~~~~~~~~~~~~~~~~~~~~~~~~~~~~~~

\begin{wrapfigure}{r}{0.35\textwidth}
	\centering
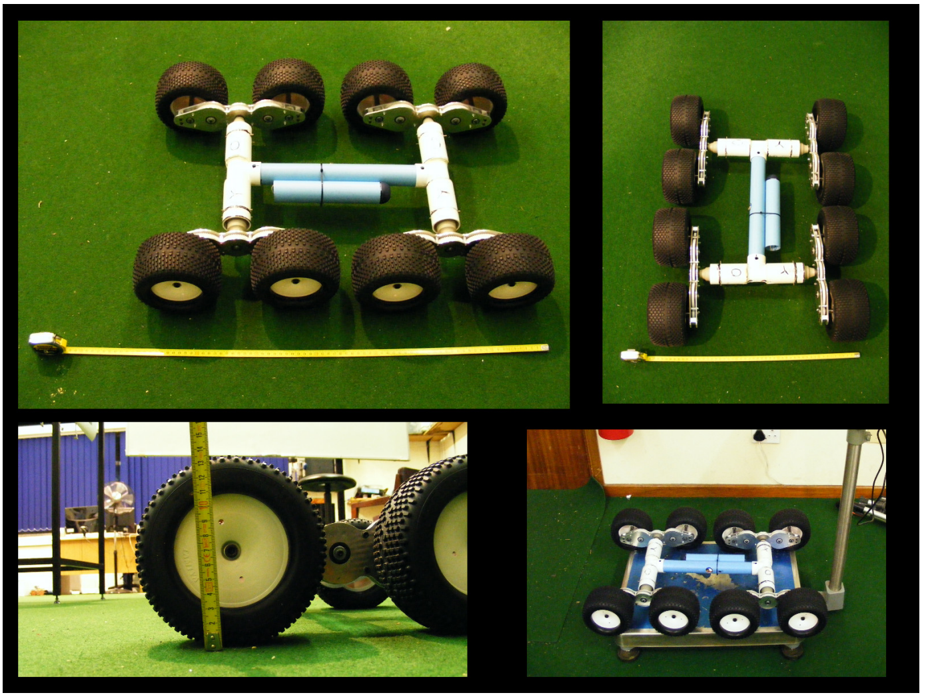
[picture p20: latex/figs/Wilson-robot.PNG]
	
	\caption{Wilson's Robot \citep{Wilson-2013}.}
	\label{Wilson robot}
\end{wrapfigure}

Wilson designed and built the first LIM robot in 2013, shown in Figure \ref{Wilson robot}. This robot was designed as a prototype for a low cost USAR stair-climbing robot. At first Wilson considered only using LIMs for the front set of wheels, with the rear set using regular wheels. However, after performing a 2D simulation in Algodoo, he concluded that using LIMs for the rear wheels was necessary as regular wheels provided little to no support to the climbing motion after the first step, presumably because the rear wheel would stop making contact with the stairs. Using LIMs for the rear wheels means they will be able to climb as well, and can always apply a forward force on the body.

\begin{wrapfigure}{l}{0.35\textwidth}
	\centering
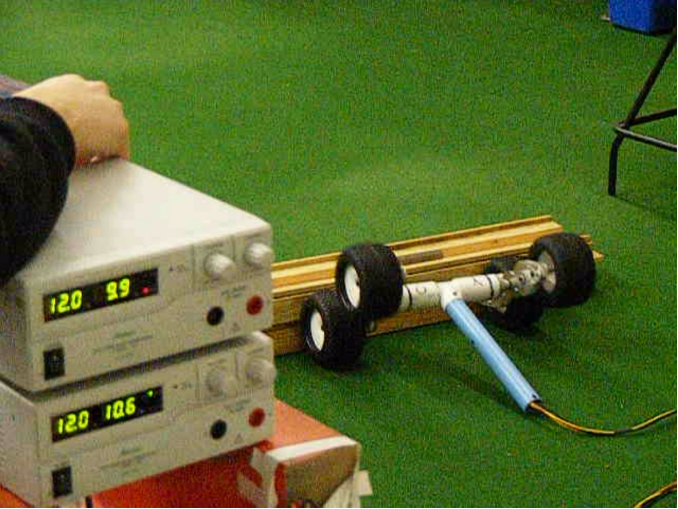
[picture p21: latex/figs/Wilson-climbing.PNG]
	
	\caption{Wilson's half assembly climbing a stair \citep{Wilson-2013}.}
	\label{Wilson climbing}
\end{wrapfigure}

Wilson's robot had some limitations that prevented him from performing extensive tests. Chiefly, it was unable to climb stairs as the motors would stall upon encountering an obstacle. To validate the LIM concept in spite of this issue, Wilson split the robot in half and tested stair climbing using only the front LIMs and the chassis dragging behind as a tail. This "tail-dragging half assembly" was able to climb a single step as shown in Figure \ref{Wilson climbing}. Wilson's project ran out of time before he was able to solve the climbing motion of the complete robot, however he was able to confirm that the LIM system can climb at least a single stair in the half assembly configuration \citep{Wilson-2013}.

\subsection{Haskel's Theseus} %~~~~~~~~~~~~~~~~~~~~~~~~~~~~~~~~~~~~~~~~~~~~~~~~~~~~~~~~~~~~~~~~~

\begin{wrapfigure}{r}{0.35\textwidth}
	\centering
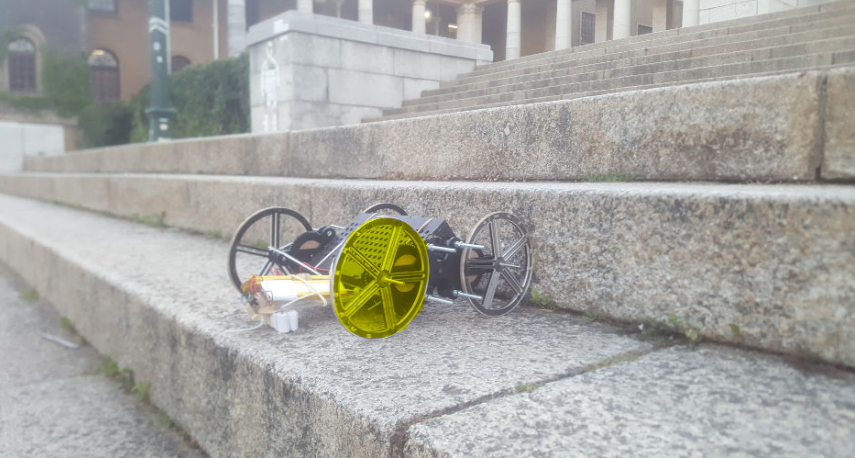
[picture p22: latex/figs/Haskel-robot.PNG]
	
	\caption{Haskel's Theseus \citep{Haskel-2017}.}
	\label{Haskel robot}
\end{wrapfigure}
Haskel designed and built a LIMed robot to further test the concept, which he named "Theseus", shown in Figure \ref{Haskel robot}. Unlike Wilson, Haskel assumes that using LIMs for rear wheels is not necessary for the stair climbing motion, and instead chooses to use a dragging tail to provide counter torque, similar to the tail-dragging half assembly used by Wilson. Theseus is much smaller and lighter than Wilson's robot.\\

Haskel tested different concepts for the tire tread, dragging tail, and gear ratios. However, none of his configurations could consistently climb a step. In the majority of step-climbing attempts, Theseus' LIMs would flip over to mount the step, but it would not be able to pull itself up. This can be attributed to a lack of grip or a lack of torque. Haskel intended to do further work on the project, however he ran out of time due to component shortages and protests at UCT \citep{Haskel-2017}.
\newpage
\subsection{Buchanan's Ascender} %~~~~~~~~~~~~~~~~~~~~~~~~~~~~~~~~~~~~~~~~~~~~~~~~~~~~~~~~~~~~~~~~~

\begin{wrapfigure}{r}{0.35\textwidth}
	\centering
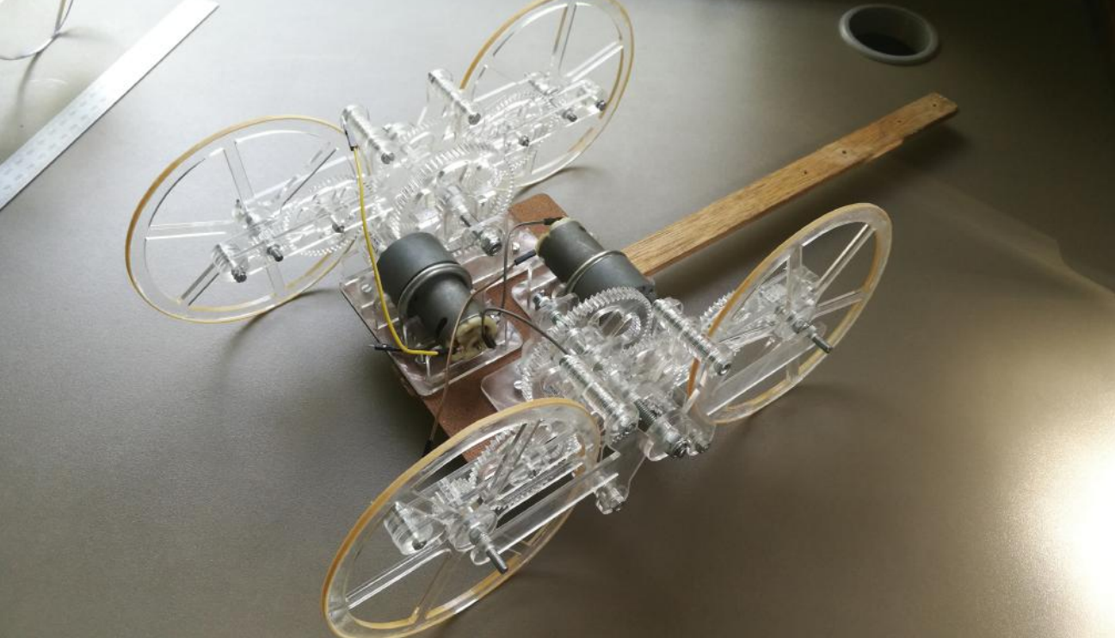
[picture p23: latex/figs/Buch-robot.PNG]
	
	\caption{Buchanan's Ascender \citep{Buchanan-2018}.}
	\label{Buch robot}
\end{wrapfigure}
Buchanan designed and built "Ascender", a robot platform using LIMs for locomotion, shown in Figure \ref{Buch robot}. Buchanan iterated on the design several times in order to reduce mass and increase torque. The intention was to build a drivetrain that could be combined with the electronics of Haskel's Theseus to produce a successful stair climbing robot. As such, the Ascender does not include any electronic control systems, and is instead controlled externally by power supplies connected to the motors.

Buchanan's testing showed that the Ascender was able to climb a single step of 120 mm in 6 out of 10 attempts, and a step of 140mm in 2 out of 10 attempts. Buchanan noted a flaw in the design; after the LIMs flip over as part of the climbing motion, the body of the robot would lodge itself onto the edge of the step and the wheels would spin freely, a phenomenon referred to as beaching. The LIMs would then spin until the top wheel makes contact with the top of the step, from there it would either grip and pull the robot up the step as intended, or it would dislodge the body and the robot would fall off the step. Buchanan also reported that the Ascender was fragile to the point that it broke during the testing. Buchanan did not test the Ascender's ability to climb a staircase, but he concluded that it would be able to as a staircase is simply repeated single steps. \citep{Buchanan-2018}

\subsection{Powrie's Di-Wheel robot}

\begin{wrapfigure}{r}{0.35\textwidth}
	\centering
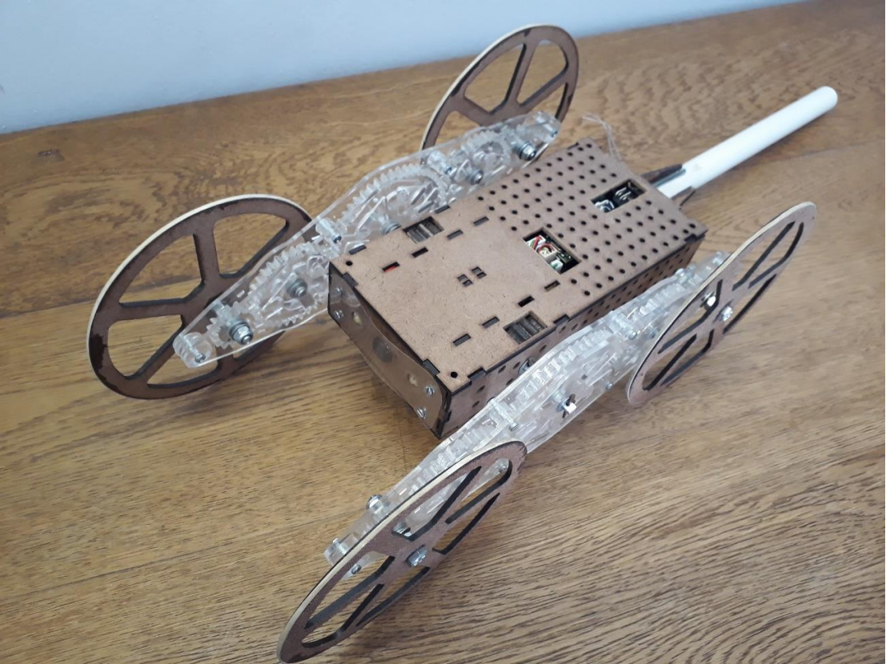
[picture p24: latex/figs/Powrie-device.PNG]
	
	\caption{Powrie's Di-Wheel Robot \citep{Powrie-2019}.}
	\label{fig:Powrie robot}
\end{wrapfigure}
Powrie developed a robot using LIMs, however in his report he referred to LIMs as Di-Wheels. His reason for renaming them is that the behaviour of the LIMs does not only respond to external loads on the wheels, it also depends on the torque applied by the motors. He chose the name "Di-Wheel" in reference to a similar design by the name of "Tri-Wheel", which used three minor wheels instead of two, developed by \cite{Smith-2015}. Powrie's Di-Wheel robot is larger and more robust than Buchanan's Ascender, while being lighter than Wilson's LIMed robot. It is shown in Figure \ref{fig:Powrie robot}.\\

The Di-Wheel robot was successful in climbing a single step of 220 mm. Further testing was not performed as noise from the robot's motors would interfere with the control system, preventing untethered driving. Powrie ran out of time before he was able to solve this issue. Powrie also found that when both motors are powered on, one of the LIMs would flip first, putting all the weight on the other LIM so preventing it from flipping. The result is that the robot would fall on its side, as seen in Figure \ref{Powrie falling} \citep{Powrie-2019}.\\
\begin{figure}[ht]
	\centering
	
	\caption{The Di-Wheel robot falling due to unsynchronised LIMs \citep{Powrie-2019}.}
	\label{Powrie falling}
\end{figure}

\subsection{Gearing} %~~~~~~~~~~~~~~~~~~~~~~~~~~~~~~~~~~~~~~~~~~~~~~~~~~~~~~~~~~~~~~~~~
%Add drawing!!
The gear ratios of the LIMs will affect its motion significantly. The rotational speed of the central gear will be translated into both the speed of the LIM frame and the speed of the wheels:
\begin{align*}
	\dot{\theta}_{\mathrm{Sun}} &= \dot{\theta}_{\mathrm{Frame}} + \frac{N_\mathrm{Planet}}{N_\mathrm{Sun}}\dot{\theta}_{\mathrm{Planet}} \tag{1}\\
\end{align*}
where $\dot{\theta}_{\mathrm{Sun}}$ is the angular speed of the central gear, $\dot{\theta}_{\mathrm{Frame}}$ is the angular speed of the LIM frame, $\dot{\theta}_{\mathrm{Planet}}$ is the angular speed of the outer gears and wheels relative to the frame, $N_{\mathrm{Planet}}$ is the number of teeth on the outer gears, and $N_\mathrm{Sun}$ is the number of teeth on the central gear.\\

When both the wheels and the LIM frame aren't constrained, the system is under-actuated and its motion is non-trivial. In the case that the LIM frame isn't flipping (i.e. normal driving on a flat plane), $\dot{\theta}_{\mathrm{Frame}} = 0$, therefore:\\
 \begin{align*}
 	\dot{\theta}_{\mathrm{Planet}} &= \frac{N_\mathrm{Sun}}{N_\mathrm{Planet}}\dot{\theta}_{\mathrm{Sun}} \tag{2}\\
 \end{align*}
When the wheels have encountered an obstacle, such as a step, friction will prevent them from turning, $\dot{\theta}_{\mathrm{Planet}} + \dot{\theta}_{\mathrm{Frame}} = 0$. In this case:
\begin{align*}
	\dot{\theta}_{\mathrm{Frame}} &= \frac{\dot{\theta}_{\mathrm{Sun}}}{(1-\frac{N_\mathrm{Planet}}{N_\mathrm{Sun}})} \tag{3}\\
\end{align*}

This means that during flipping motion, if $\frac{N_\mathrm{Planet}}{N_\mathrm{Sun}} > 1$, then the LIM frame will flip in the opposite direction to the rotation of the central gear, so the front wheel will roll up the side of the obstacle \citep{Wilson-2013}. This is ineffective for climbing steps as the LIM will never mount the step, but rather continue rotating backwards until it returns to the starting position \citep{Haskel-2017}.\\

\begin{figure}[h]
	\centering
	
	\caption{Two different climbing motions using different gear ratios \citep{Powrie-2019}.}
	\label{Powrie gears}
\end{figure}

If $\frac{N_\mathrm{Planet}}{N_\mathrm{Sun}} < 1$, then the LIM frame will rotate forward, the rear wheel will flip over and mount the obstacle. This allows the LIM to climb stairs as intended.\\
The two cases are shown in Figure \ref{Powrie gears}, with the left showing the case when $\frac{N_\mathrm{Planet}}{N_\mathrm{Sun}} < 1$, and the right showing the case when $\frac{N_\mathrm{Planet}}{N_\mathrm{Sun}} > 1$.

%\subsection{Control requirements} %~~~~~~~~~~~~~~~~~~~~~~~~~~~~~~~~~~~~~~~~~~~~~~~~~~~~~~~~~~~~~~~~~
%
%LIMs are considered "Load intuitive" because of their ability to adapt to terrain mechanically. Open-loop control is ideal in this case, as an operator need only turn the motor on and the LIM will drive forward if it can, or attempt to climb an obstacle if it is obstructed \citep{Wilson-2013}. However, Powrie found that his robot was not suited to open loop control. When full voltage is provided to the motor, the LIMs would flip even if when is on a flat plane. Powrie's calculations suggest that whether the LIM flips or not is largely dependent on the torque applied to it. A low torque results rolling, and a high torque results in flipping. His report suggests that LIMs only responds to terrain intuitively for a "medium torque" \citep{Powrie-2019}. In this case a medium torque would be defined as a torque that results in rolling when the LIM is unobstructed, and flipping only when it is obstructed. This indicates that it may be necessary to have a control system that manages the torque provided to the LIMs to ensure that they do not flip on flat terrain if the motors are sufficiently powerful.\\
%
%Powrie also found that when climbing a step, one LIM could flip first, putting weight on the other and preventing it from flipping, as seen previously in Figure \ref{Powrie falling} \citep{Powrie-2019}. This suggest that a control system is needed to roughly synchronise the LIMs, if one is ahead of the other, more torque should be provided to the trailing LIM to correct its motion.

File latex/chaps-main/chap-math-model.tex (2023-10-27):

\chapter{Maths Model}

\section{Overview and objectives}

This project develops a system of equations to analytically model the climbing motion of the device, which will be referred to as the "maths model" henceforth. The intention behind this model is to allow designers to input parameters such as gear ratio, mass, wheel size, tail length, and motor torque, and then determine whether the specified device will be able to climb steps. The equations can also be reversed to solve for specific parameters, such as the motor torque required to lift a device with certain properties. The maths model is developed using the MATLAB symbolic toolbox \citep{matlab}.\\

\section{Definition of motions}

As a LIMed device climbs, the tail and wheels come into contact with different surfaces on the stairs and ground, which changes how the device moves. The overall climbing motion is broken down into sequential stages which are modelled individually. These stages are defined as follows:\\
\subsection*{Stage 0: Rolling}

When the LIMed device is on a flat plane with no obstacle, it simply rolls forward. If the motor torque is high enough, the LIMs will flip even without an obstacle. However, DC motors lose torque as they gain speed, so the rolling motion prevents the motors from producing enough torque to flip the LIMs.\\

\subsection*{Stage 1: Lifting}
\begin{wrapfigure}{r}{0.35\textwidth} %this figure will be at the left
	\centering
	
	\caption{Stage 1 motion.}
	\label{fig:stage1}
\end{wrapfigure}
When the front wheels of the LIMs come into contact with the first step, they are blocked by a step and fixed in place. The tail pushes against the ground and the LIMs start rotating up the step. This motion ends when the LIMs are vertical.
\\
\subsection*{Stage 2: Flipping}
\begin{wrapfigure}{r}{0.35\textwidth} %this figure will be at the left
	\centering
	
	\caption{Stage 2 motion.}
	\label{fig:stage2}
\end{wrapfigure}
Once the LIMs are vertical, the bottom wheels start to roll backwards as the top wheels fall forward onto the step. The distance that the bottom wheels roll depends on the speed of the LIMs and the height of the step. If the frames of the LIMs hits the edge of the step, the device may slip backwards until the top wheel makes contact with the step. This motion ends when the top wheel is on the step.\\

\subsection*{Stage 3: Climbing}
\begin{wrapfigure}{r}{0.35\textwidth} %this figure will be at the left
	\centering
	
	\caption{Stage 3 motion.}
	\label{fig:stage3}
\end{wrapfigure}
The front wheel rests on the step while the back wheel is on the ground. The tail pushes against the ground and the back wheel lifts while the front wheel simultaneously rolls forward on the step. This motion ends when the front wheel reaches the next step.\\

Stages 1 to 3 will repeat until the tail leaves the ground. After this point the tail will push against the edge of the previous steps. The number of steps the device must climb before the tail leaves the ground will depend on the length of the tail, the size of the other components, and the size of the steps. 

\subsection*{Stage 4: Lifting from step}
\begin{wrapfigure}{r}{0.35\textwidth} %this figure will be at the left
	\centering
	
	\caption{Stage 4 motion.}
	\label{fig:stage4}
\end{wrapfigure}
Similar to Stage 1, but the tail pushes against the edge of a previous step, which now applies a force pulling the device backwards. Assuming friction on the wheel is sufficient, the LIMs start rotating up the step. This motion ends when the LIMs are vertical.

\subsection*{Stage 5: Flipping from step}

Similar to Stage 2, but the tail pushes against the edge of a previous step, which now applies a force pulling the device backwards. This motion ends when the top wheel is on the step.\\
\begin{figure}[!h] %this figure will be at the left
	\centering
	
	\caption{Stage 5 motion.}
	\label{fig:stage5}
\end{figure}
\subsection*{Stage 6: Climbing from step}

\begin{wrapfigure}{r}{0.35\textwidth} %this figure will be at the left
	\centering
	
	\caption{Stage 6 motion.}
	\label{fig:stage6}
\end{wrapfigure}

Similar to Stage 3, but the tail pushes against the edge of a previous step, which now applies a force pulling the device backwards. The back wheel lifts while the front wheel rolls forward on the step. This motion ends when the front wheel reaches the next step.\\

\section{Core equations and assumptions}

The maths model is a system of equations that are solved simultaneously. These equations are derived from the free body diagrams of each component, and only consider movement in two dimensions. The components in question are the LIM frame, the sun gear, the idler gears, and the planet gears including the shaft and the wheels, and the body of the device. These components make contact with the surroundings and the other components, which exert equal and opposite forces on each other. As the maths model only considers movement in two dimensions, the LIMs are assumed to move synchronously. To simplify the equations, only one LIM is modelled, and its mass and moment of inertia is doubled.\\

Consider the device climbing a step as visualised in Figure \ref{Component-names}. Each component is assigned a number, where the LIM frame is 1, the sun gear is 2, the idler gears are 3 and 4, the planet gears, including the wheels, are 5 and 6, and the body of the device, including the tail, is 7.
\begin{figure}[h]
	\centering
	
	\caption{Labelled components.}
	\label{Component-names}
\end{figure}
Powering the motor causes a torque between the body of the device and the sun gear. The components of the device that make contact with the environment, namely the front wheel and the tail, will be subject to external reaction forces, which are dependent on the stage of motion. These forces and torques will propagate internally through the gears, causing a forward motion. The free body diagrams for each component are shown in Figures \ref{FBD-1} and \ref{FBD-2}.\\
\begin{figure}[h]
	\centering
	
	\caption{Free body diagram of the LIM frame (component 1).}
	\label{FBD-1}
\end{figure}
\begin{figure}[!h]
	\centering
	
	\caption{Free body diagram of the gears (components 2-5).}
	\label{FBD-2}
\end{figure}

Each component exerts a force on connected components, which exert an equal and opposite force back.
For example, the sum of forces equations for the sun gear are,\\
\begin{equation}
	m_2\vec{a_2} = \vec{w_2}-\vec{f_2}+\vec{\mathrm{gf}_3}+\vec{\mathrm{gf}_4}
\end{equation}
Where $m_n$ refers to the mass of component $n$, $\vec{a_n}$ is the acceleration vector of component $n$, $\vec{w_n}$ is the weight vector of component $n$, $\vec{f_n}$ is the force vector that component $n$ applies to component 1,  and $\vec{\mathrm{gf}_3}$ and $\vec{\mathrm{gf}_4}$ are the force vectors that components 3 and 4 respectively apply to component 2 through the gears.
This can be expanded to,
\begin{equation}
	m_2
	\begin{bmatrix}
		a_{2x}\\
		a_{2y}\\
		a_{2z}\\
	\end{bmatrix}
	=
	\begin{bmatrix}
		w_{2x}-f_{2x}+\mathrm{gf}_{3x}+\mathrm{gf}_{4x}\\
		w_{2y}-f_{2y}+\mathrm{gf}_{3y}+\mathrm{gf}_{4y}\\
		w_{2z}-f_{2z}+\mathrm{gf}_{3z}+\mathrm{gf}_{4z}\\
	\end{bmatrix}
\end{equation}
where vector positions 1, 2, and 3 denote the x, y, and z dimensions respectively. This equation can be further simplified by restraining movement to the x and y dimensions, and substituting $\vec{w_2} = \begin{bmatrix} 0 \\ m_2g & \\ \end{bmatrix}$,
\begin{equation}
	m_2
	\begin{bmatrix}
		a_{2x}\\
		a_{2y}\\
	\end{bmatrix}
	=
	\begin{bmatrix}
		-f_{2x}+\mathrm{gf}_{3x}+\mathrm{gf}_{4x}\\
		m_2g-f_{2y}+\mathrm{gf}_{3y}+\mathrm{gf}_{4y}\\
	\end{bmatrix}
\end{equation}
Similarly, the sum of moments equation for the sun gear is derived
\begin{equation}
	I_2\ddot{\theta_2} = T - r_2|\vec{\mathrm{gf}_3}| + r_2|\vec{\mathrm{gf}_3}|
\end{equation}
where $I_2$ is the moment of inertia of component 2, $\theta_2$ is the angle of component 2, $T$ is the moment exerted by the motor on component 2, and $r_2$ is the radius of component 2. Note that in this project, all angles and moments are given in the clockwise direction.
\\
The full list of equations can be found in MATLAB/Core\_equations.mat in the project repository \citep{repo}.

\section{Boundary conditions}
Depending on the stage of the climbing, components of the device will come into contact with different parts of the steps and at different angles. To model climbing in each stage, a set of equations defining the contact is given for each stage.\\
\subsection*{Stage 1: Lifting}
The front wheel, referred to as component 5, is locked in place by the reaction forces from the step, this leads to the condition,
\begin{subequations}
	\label{wheel1locked}
	\begin{align}
		\vec{a_5} &= \vec{0}\\
		\vec{v_5} &= \vec{0}\\
		\dot{\theta}_5 &= 0\\
		\ddot{\theta}_5 &= 0
	\end{align}
\end{subequations}
where $\vec{v_n}$ refers to the velocity of component $n$. \\
The front wheel must be placed into a two-dimensional coordinate system. In Stage 1, the front wheel can be on the ground or on one of the steps, so long as the tail can reach the ground, and the front wheel will always be pressed against the edge of the next step. Placing the origin at the start of the steps, the position of the front wheel can be defined as,
\begin{equation}
	\vec{s_5}
	=
	\begin{bmatrix}
		\mathrm{StepWidth}\cdot N-r_w\\
		\mathrm{StepHeight}\cdot N+r_w\\
		0
	\end{bmatrix}
\end{equation}
where $\vec{s_5}$ is the position vector of the centre of the front wheel, $N$ is the number of the step on which the wheel is placed, with $N = 0$ placing the step on the ground, and $r_w$ is the radius of the wheel.\\
The end of the tail pushes against the ground, which leads to the following conditions,
\begin{subequations}
	\label{tailonground}
	\begin{align}
		s_{7\mathrm{end}y} &= 0\\
		F_{\mathrm{React}7x} &=  -\mu_{\mathrm{tail}}F_{\mathrm{React}7y}\\
		-\ddot{\theta_7} &= \frac{(|\vec{l_7}|^2 - l_{7y}^2)a_{1y} + l_{7y}v_{1y}^2}{|\vec{l_7}|^3 (1 - \frac{l_{7y}^2}{|\vec{l_7}|^2})^{3/2}} \label{tailongroundkinematics}
	\end{align}
\end{subequations}
where $s_{7\mathrm{end}y}$ is the y position of the endpoint of the tail, $F_{\mathrm{React}7x}$ and $F_{\mathrm{React}7y}$ are the reaction forces exerted onto the tail by the ground in the x and y dimensions respectively, $\mu_{\mathrm{tail}}$ is the coefficient of friction between the tail and the ground, $\vec{l_7}$ is the position of the end of the tail relative to the motor axle, and $l_{7y}$ is the component of $\vec{l_7}$ in the y dimension. \\
Equation \ref{tailongroundkinematics} is derived from,

\begin{subequations}
	\begin{align}
		-\theta_7(t) &= \arcsin{\frac{l_{7y}(t)}{|\vec{l_7}|}}\\
		\frac{d^2}{dt^2}-\theta_7(t) &= \frac{d^2}{dt^2}\arcsin{\frac{l_{7y}(t)}{|\vec{l_7}|}}
	\end{align}
\end{subequations}
where $\theta_7$ and $l_{7y}$ are treated as functions of time, $t$. This relation can be seen in Figure \ref{fig:tailGround}. $v_{1y}$ and $a_{1y}$ refer to the velocity and acceleration of the motor axle in the y dimension, and are equivalent to $-\dot{l}_{7y}$ and $-\ddot{l}_{7y}$ respectively. These equations assume that the width of the tail is negligible.\\

\begin{figure}[!h]
	\centering
	
	\caption{Definition of $\vec{l}_7$ and $\theta_7$.}
	\label{fig:tailGround}
\end{figure}

\subsection*{Stage 2: Flipping}

Once the LIM is vertical, there is no longer a force pushing the bottom wheel forward into the step, instead it rolls backwards. This leads to a new condition,
\begin{subequations}
	\label{wheel1rolling}
	\begin{align}
		\vec{a_5} &= \begin{bmatrix}
			\ddot{\theta}_5 r_w \\
			0\\
			0
		\end{bmatrix}\\
		\vec{v_5} &= \begin{bmatrix}
			\dot{\theta}_5 r_w \\
			0\\
			0
		\end{bmatrix}\\
		s_{5x} &= \theta_{5} r_w;\\
		M_{\mathrm{React}5} &= - F_{\mathrm{React}5x} r_w;
	\end{align}
\end{subequations}
where $M_{\mathrm{React}5}$ is the reaction moment on wheel 5 as a result of the reaction forces.
The tail is still on the ground, so will still be subject to Equations \ref{tailonground}.

\subsection*{Stage 3: Climbing}

In Stage 3, the front and back wheel have swapped. To simplify the movements, component 5 will always refer to the wheel that makes contact with the steps, and component 6 will refer to the wheel that does not. \\
The front wheel is rolling and the tail is on the ground, which are the same conditions as in Stage 2. As such, Stage 3 is subject to Equations \ref{wheel1rolling} and \ref{tailonground}.

\subsection*{Stage 4: Lifting with tail on step}
Stage 4 is similar to Stage 1, except the tail is on the step. As such, this motion is subject to Equations \ref{wheel1locked} because the wheel is locked, and a set of new conditions because the tail is on the edge of the step,

\begin{subequations}
	\label{tailonstep}
	\begin{align}
		u_x &= \mathrm{StepWidth}\cdot (N_2-1)- s_{1x}\\
		u_y &= \mathrm{StepHeight}\cdot N_2 - s_{1y}\\
		\tan{(-\theta_7)} &= \frac{u_y}{u_x}\label{tailonstepposition}\\
		\begin{split}
		-\ddot{\theta_7} &= \frac{1}
		{(u_x^2 + u_y^2)^2}
		\Big( u_x^2 (a_{1x} u_y  - 2 v_{1x} v_{1y})
		+ u_y^2 (a_{1x} u_y + 2  v_{1x}  v_{1y}  )  \: ...\\
		&\;\;\;\;\;-  a_{1y} u_x^3 
		- u_x  u_y  (- 2  v_{1x}^2 + 2 v_{1y}^2 + a_{1y} u_x  )\Big)
		\end{split}
		\label{tailonstepaccelleration}\\
		F_{\mathrm{React}7x}' &= -\mu_{\mathrm{tail}} F_{\mathrm{React}7y}'\\
		\vec{F}_{\mathrm{React}7} &= \begin{bmatrix}
			-\cos{(\theta_7)} & -\sin{(\theta_7)} & 0\\
			\sin{(\theta_7)} & -\cos{(\theta_7)} & 0\\
			0 & 0 & 1
		\end{bmatrix} \vec{F}_{\mathrm{React}7}'
	\end{align}
\end{subequations}
where $N_2$ is the number of the step that the tail makes contact with, $\mathrm{StepWidth}$ and $\mathrm{StepHeight}$ are the width and height of each step in the stairs, $u_x$ and $u_y$ are the displacement from the motor axis to the point of contact between the tail and the step. Equation \ref{tailonstepaccelleration} is the second derivative of \ref{tailonstepposition}. $\vec{F}_{\mathrm{React}7}'$ is the vector of reaction forces in a rotated coordinate system such that $F_{\mathrm{React}7y}'$ is the normal force between the tail and the step.

\subsection*{Stage 5: Flipping from step}
Stage 5 is similar to Stage 2, except the tail is on the step. As such, this motion is subject to Equations \ref{wheel1rolling} because the wheel is locked, and Equations \ref{tailonstep} because the tail is on the step.\\

\subsection*{Stage 6: Climbing from step}
Stage 6 is similar to Stage 3, except the tail is on the step. As such, this motion is subject to Equations \ref{wheel1rolling} because the wheel is locked, and Equations \ref{tailonstep} because the tail is on the step.\\

\section{Solving technique}
The MATLAB symbolic toolbox comes with the solve() function, which can be used to solve sets of non-linear simultaneous equations. However, it struggles with this large set of equations that contain trigonometric functions, often stalling. This project develops a function that breaks down the set of equations into smaller, easier to solve sets, then substitutes these solutions into the remaining equations. Figure \ref{fig:solver-flowchart} shows the flowchart for this function. \\

\begin{figure}[!!h]
	\centering
	
	\caption{Flowchart for this project's solver.}
	\label{fig:solver-flowchart}
\end{figure}
The function loops through the equations until they have all been solved, or it cannot find any more solutions. First, it identifies any trivial equations that contain only one variable, such as $a = 1$, and solves them. This will also pick up equations with more than one solution, such as $\sin(a) = 1$; to resolve this, the solver will look for inequalities that contain the relevant variable, in this case $a$, and apply them to the solution. For example, if you were to provide the function with the set of equations:\\

\begin{subequations}
	\label{exampleinput}
	\begin{align}
		a &= 0.5 \label{example1a}\\
		\sin{(b)} &= a\\
		b &>= \frac{\pi}{2}\\
		b &<= \pi
	\end{align}
\end{subequations}
The first loop would identify Equation \ref{example1a} as it only has one variable. It wouldn't find any inequalities that describe the variable $a$ so it would simply send the equation $a = 0.5$ to MATLAB's solve() function. It then records the solution and substitutes it into the remaining equations, 
\begin{subequations}
	\label{example2}
	\begin{align}
		\sin{(b)} &= 0.5 \label{example2a}\\
		b &>= \frac{\pi}{2}\label{example2b}\\
		b &<= \pi\label{example2c}
	\end{align}
\end{subequations}
The second loop identifies Equation \ref{example2a} as it only has one variable. It looks for inequalities that describe $b$ and finds Inequalities \ref{example2b} and \ref{example2c}. It then sends all three to MATLAB's solve() function, which returns the solution for $b$.
The function then outputs a structure with the fields,
\begin{subequations}
	\begin{align}
		\mathrm{solution.a} &= 0.5\\
		\mathrm{solution.b} &= \frac{5\pi}{6}
	\end{align}
\end{subequations}

Once the function can no longer find trivial solutions, it looks for sets of equations that contain the exact same variables, such as equations of the form,
\begin{subequations}
	\begin{align}
		a -2b &= 0\\
		b -a +2 &= 0 
	\end{align}
\end{subequations}
and sends them to be solved. For this to work, there must be at least as many equations as there are variables in the set. This function will also identify and delete duplicate equations.\\
Once the function can no longer find sets of equations that use the exact same variables, it will attempt to find sets of equations that fully describe a set of variables, such as,
\begin{subequations}
	\begin{align}
		a -3b &= 0\\
		b -c +2&= 0\\
		a -2c &= 0
	\end{align}
\end{subequations}
Finally, if it can't find any fully defined sets up to a certain size, it will attempt to solve the complete set of remaining equation using the solve() function. If the function is unable to solve all the equations, it will return a structure containing the solutions it has found, and a vector containing the remaining equations. This is useful for debugging as it provides feedback on which variables it did and did not have enough information to solve for, something the MATLAB solve() function does not do.\\

\section{Required torque}
When designing a LIM robot, it is essential to size the motor and gearbox to be able to provide enough torque to lift the LIMs. To do this, one must first determine which stage of motion requires the most torque. To find the minimum torque required to cause forward movement, we solve for the torque that results in an overall acceleration of 0 when the velocity is also 0, essentially adding the conditions:
\begin{subequations}
	\label{condition-static}
	\begin{align}
		\vec{a} &= \vec{0}\\
		\vec{v} &= \vec{0}\\
		\ddot{\theta_1} &= 0\\
		\dot{\theta_1} &= 0\\
	\end{align}
\end{subequations}
which simplifies the dynamic equations into static equations.\\
The set of equations is then solved for a range of positions in each stage. The required torque across the full range of motion is shown in Figure \ref{fig:bigplot}, along with illustrations of the device as it transitions between stages of motion. Figure \ref{fig:bigplot} shows that the highest torque is needed for the Stage 4 motion.\\

\begin{figure}[h]
	\centering
	
	\caption{Relationship between LIM angle and required torque across all stages of motion.}
	\label{fig:bigplot}
\end{figure}

During Stages 1 and 4, the required torque increases slightly as the LIM lifts up from horizontal, then rapidly decreases as the LIM approaches vertical. During Stages 2 and 5, the LIM simply falls down onto the next step, so no motor torque is required. During Stages 3 and 6, the required motor torque gradually increases as the back wheel of the LIM lifts and the front wheel rolls to the next step. 

\section{Required coefficient of friction}

When the device climbs steps, it is possible that the front wheel, component 5, will slip. Slipping can cause the device to be unable to climb stairs, and the maths model works under the assumption that there is no slipping. Applying the Coulomb approximation of friction to the model, slipping will occur when $|F_{5x}| > \mu_5 F_{5y}$, where $\mu_5$ is the coefficient of friction between the wheel and the step. This coefficient can be increased by using certain materials, such as rubber, for the contact surface of the wheels. However, the coefficient of friction is also dependent on the material of the step itself, which a designer would not have control over. For this reason, designers may want to modify the design to reduce the required coefficient of friction.\\
Similar to the required torque, the coefficient of friction required to prevent slipping can also be calculated across the motion, and the highest value is in Stage 4, as seen in Figure \ref{bigplot-grip}.

\begin{figure}[h]
	\centering
	
	\caption{Relationship between LIM angle and required coefficient of friction.}
	\label{bigplot-grip}
\end{figure}

\section{Using the model to size components}
So far this section has only modelled a device with fixed parameters, such as gear ratio, wheel size, mass, and tail length, however a designer may be interested in varying these parameters. The model can be used to inform the design process by showing the effect that changing certain parameters has on the required torque and the required coefficient of friction. Both of these requirements are highest in Stage 4. For example, Figures \ref{fig:GR-torque} and \ref{fig:GR-friction} show how changing the gear ratio affects the required torque and required coefficient of friction respectively.\\

\begin{figure}[h]
	\centering
	
	\caption{Relationship between LIM gear ratio and required torque.}
	\label{fig:GR-torque}
\end{figure}
\begin{figure}[h]
	\centering
	
	\caption{Relationship between LIM gear ratio and required coefficient of friction.}
	\label{fig:GR-friction}
\end{figure}
These plots show that maximising the ratio between the sun and planet gears will reduce the amount of torque required from the motor to allow forward movement, and allow the device to climb without slipping on a larger range of surfaces. Interestingly, increasing the gear ratio will also allow the device to move faster when rolling without obstructions. This provides a useful insight for design, the device will be faster, need a less powerful motor, and slip less often with a higher gear ratio.

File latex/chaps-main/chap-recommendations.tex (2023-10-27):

\chapter{Recommendations for future work}

This project was successful in building a LIMed device that can climb stairs. However, the device does have some limitations. It cannot turn easily, and it relies on an external power source. The logical next steps in the development of LIM robots would be to find a way to improve the turning ability of the device, and to design a device that can be operated remotely. Such a device could then be tested for applicability in USAR environments.

\section{Recommendation for design}

When designing a device that uses LIMs, this project recommends first using the maths model to inform the selection design parameters. This can be done by changing a parameter and noting how it affects the performance of the design, similar to what was done in Figure \ref{fig:GR-friction}. Once the design parameters have been selected, the device should be designed in CAD and converted to SDFormat. From there the device can be simulated using Drake, and if performance is satisfactory, it can be built. Instructions on how to perform each of these steps can be found in the project repository \citep{repo}.\\

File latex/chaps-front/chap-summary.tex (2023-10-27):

\chapter{Executive summary}

\noindent
\begin{longtable}{|p{\dimexpr \linewidth-2\tabcolsep-2\arrayrulewidth}|}
\hline%------------------------------------------------------------
\sumheading  Title of Project \\
\hline%------------------------------------------------------------
 Design, model and build a USAR robot platform \\
\hline%------------------------------------------------------------
\sumheading  Objectives \\
\hline%------------------------------------------------------------
 Create a model to describe the kinematics of a Load Intuitive Module (LIM). \\
 Build a prototype Urban Search and Rescue (USAR) device which uses LIMs to climb stairs.\\
 Validate the model using the prototype.\\
\hline%------------------------------------------------------------
\sumheading  What is current practice and what are its limitations? \\
\hline%------------------------------------------------------------
 The current practice for USAR platform ranges widely, but the most successful platforms use tracks with paddles for locomotion.
 These devices are effective but very expensive, so there is a need for low cost expendable USAR robots.\\
\hline%------------------------------------------------------------
\sumheading  What is new in this project? \\
\hline%------------------------------------------------------------
 This project will introduce a model to describe a less expensive stair climbing robot platform using LIMs. \\
 
\hline%------------------------------------------------------------
\sumheading  If the project is successful, how will it make a difference? \\
\hline%------------------------------------------------------------
 The model developed in this project can be used to inform future USAR designs. \\

\hline%------------------------------------------------------------
\sumheading  What are the risks to the project being a success? Why is it expected to be successful? \\
\hline%------------------------------------------------------------
 The main risk to this project is that it does not build a working prototype in time. This risk will be mitigated through careful planning and consideration of previous pitfalls.  \\

\hline%------------------------------------------------------------
\sumheading  What contributions have/will other students made/make? \\
\hline%------------------------------------------------------------
 In 2013, Matthew Wilson developed the LIM system as a masters project at the University of Cape Town (UCT).
 Further development on the system was done in final year projects at UCT by students Jordan Haskel, Murray Buchanan, and Richard Daniel Powrie in 2017, 2018, and 2019 respectively.\\
\hline%------------------------------------------------------------
\sumheading  Which aspects of the project will carry on after completion and why? \\
\hline%------------------------------------------------------------
 USAR devices using LIMs as a platform can be designed using the model presented in this project.\\

\hline%------------------------------------------------------------
\sumheading  What arrangements have been/will be made to expedite continuation? \\
\hline%------------------------------------------------------------
 All calculations, designs, and code will be made available to future students. \\

\hline%------------------------------------------------------------
\end{longtable}

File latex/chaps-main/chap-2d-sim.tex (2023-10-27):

\chapter{Two-dimensional simulation}

In order to create an accurate model of the LIM system, it is important to understand how it functions. Previous reports have given some insight into this, but none of them have demonstrated a LIM robot that can climb consecutive steps. Wilson performed a simple simulation of a LIM robot in Algodoo, and concluded that the robot would need LIMs for the rear wheels in order to support consecutive stair climbing \citep{Wilson-2013}, however all of the subsequent projects simply used a dragging tail instead of rear wheels. There is a need to resolve this inconsistency in past work, and to gain insight into the function of the LIM system. To do this, another 2D simulation using Algodoo is performed.

\section{Limitations}

Algodoo is a two-dimensional physics sandbox \citep{Algodoo}. Initial testing with the software showed that limitations on the physics engine prevent accurate simulation of gears with teeth at a centimetre scale. This means it is impossible to accurately simulate a LIM device at the scale that they would be used in reality. The simulation can be scaled up to avoid this issue. However, this prevents an accurate simulation of the kinematics of the system.\\

Additionally, it was found that Algodoo does not allow for the accurate simulation of an electric motor. In a typical electric motor, the available torque will decrease as the speed increases. This nuance is not present in Algodoo, so it cannot be used to provide an accurate simulation of the motor requirements. Despite these limitations. Algodoo is still useful as a tool to roughly test the motion of LIMs, and to determine how it would interact with steps. The advantage of Algodoo over other simulation methods is its ease of use, it only takes a few minutes to build a LIMed robot in Algodoo.

%\section{Configuration}

%To improve the accuracy of the Algodoo physics engine, the simulation frequency is set to 1200 and all objects are scaled up 100 times. A basic LIM system with a dragging tail is set up, using gear and wheel dimensions from \cite{Powrie-2019}, shown in Figure \ref{algo-model}.

%\begin{figure}[h]
%	\centering
%	\includegraphics[width=0.8\textwidth]{algo-model}
%	\caption{Initial Algodoo LIM system}
%	\label{algo-model}
%\end{figure}
\section{Observations}

Simulations suggest that using a second set of LIMs as rear wheels is not necessary for successful consecutive stair climbing. If the motor torque is sufficient, the LIM will be able to climb steps with only a dragging tail for counter torque.\\

There are three ways in which a LIM can mount an obstacle after flipping up to it. The first is that the wheel collides directly with the obstacle, shown in Figure \ref{algo-case-wheel}. This happens when the obstacle is taller than a certain threshold based on the geometry of the LIM, and can result in the wheel bouncing off the obstacle and failing to pull itself up. In this case a controller may be used to limit the speed of the flipping motion to ensure that the wheel is not going fast enough to bounce off the obstacle when it collides. \\
%\begin{wrfigure}{r}{0.4\textwidth} %this figure will be at the left
%	\centering
%	\includegraphics[width=0.4\textwidth]{algo-case-wheel}
%	\caption{LIM climbing with wheel contact}
%	\label{algo-case-wheel}
%\end{wrfigure}
%
%\begin{wrapfigure}{r}{0.4\textwidth} %this figure will be at the left
%	\centering
%	\includegraphics[width=0.4\textwidth]{algo-case-frame}
%	\caption{LIM climbing with LIM frame contact}
%	\label{algo-case-frame}
%\end{wrapfigure}

The second way is that the LIM frame collides with the obstacle and mounts it, then the LIM continues to rotate until the wheel makes contact with the surface of the obstacle to pull the robot forward. This case is shown in Figure \ref{algo-case-frame}. Note that the LIM frame can slip on the edge of the obstacle, which may result in failure to climb. \\
\begin{figure}
	\centering
	\begin{subfigure}{.5\textwidth}
		\centering
		
		\caption{Wheel contact}
		\label{algo-case-wheel}
	\end{subfigure}%
	\begin{subfigure}{.5\textwidth}
		\centering
		
		\caption{LIM frame contact}
		\label{algo-case-frame}
	\end{subfigure}
	\caption{LIM climbing with wheel contact and LIM frame contact.}
	\label{fig:algo-climbing}
\end{figure}

\begin{wrapfigure}{r}{0.4\textwidth} %this figure will be at the left
	\centering
	
	\caption{LIM climbing with robot body contact.}
	\label{algo-case-body}
\end{wrapfigure}

The third way is that the body of the robot, presented here as an extension of the tail, will mount the obstacle. This is shown in Figure \ref{algo-case-body}.
When the body has beached onto the obstacle, seen in Figure \ref{algo-case-body}.2, there is nothing resisting the motion of either the wheels or the LIM, so they can accelerate quite quickly. If they move too fast, the wheel can bounce off the obstacle when it makes contact, dislodging the body so that it falls back down to the initial position. \cite{Buchanan-2018} found that his Ascender followed this motion, which caused it to fail many of its climbing tests. He mentions that this can be avoided by moving the LIM axle to the end of the body, so that the body does not protrude beyond the LIM frame during climbing motion.\\

%Each of these climbing methods has its flaws, however the case where the LIM frame collides with the obstacle is preferred as it reduces the chance that the wheel will bounce off the obstacle. To address slipping, grousers can be added to the robot's body \citep{rob2014}. The updated model with grousers can be seen in Figure \ref{algo-model2}.\\

%\begin{figure}[h]
%	\centering
%	\includegraphics[width=0.8\textwidth]{algo-model2}
%	\caption{Algodoo LIM system with grousers on frame}
%	\label{algo-model2}
%\end{figure}

%\subsection{Rolling and flipping}

%It was observed in simulation that the LIM would either roll or flip depending on the torque applied to it. There appeared to be a very small range of "medium torque" at which the LIM was truly load intuitive. If the motor torque was too weak it would never be able to flip over the obstacle and if it was too strong it would always flip and never roll, which hinders movement on flat terrain. However, this may simply be a result of inaccuracies of the simulation, as scaling and poor motor physics could significantly affect this motion. \\

%In reality, as an electric motor increases in speed, the torque available will decrease proportionally. This means that once the LIM is rolling at speed, it will no longer have enough torque to flip itself unless it is stopped by an obstacle. This suggests that too much torque will only cause unintended flipping when the LIM is at rest on a flat plane.\\

%\begin{figure}[h]
%	\centering
%	\includegraphics[width=1\textwidth]{algo-hori}
%	\caption{Algodoo LIM system approaching obstacle horizontally}
%	\label{algo-hori}
%\end{figure}

%\begin{figure}[h]
%	\centering
%	\includegraphics[width=1\textwidth]{algo-vert}
%	\caption{Algodoo LIM system approaching obstacle vertically}
%	\label{algo-vert}
%\end{figure}

%Another observation made was that if the LIM rolls at speed into the obstacle, it will have to absorb all the energy of the impact. None of the translational kinetic energy of the robot is transformed into rotational kinetic energy of the LIM for flipping. This results in quite an inefficient system. One option to mitigate this would be to implement a control system that solves the inverted pendulum problem in order to stand the LIMs upright on one wheel during normal operation. When the lower wheel encounters an obstacle while rolling, the LIM will readily flip over it without having to stop. The LIM could then switch to horizontal rolling when the robot needs a lower profile to enter a void. This solution would only be effective if a robust control system can be developed. These approaches are shown in Figures \ref{algo-hori} and \ref{algo-vert}.

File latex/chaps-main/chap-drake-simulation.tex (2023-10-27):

\chapter{Drake Simulation}

\section{Overview and objectives}

Instead of building a set of equations to simulate a robot from scratch, designers can use existing tools to simplify and streamline the modelling of a robot's movement. One such tool is rigid body simulation, which involves placing objects in a simulated environment and modelling the weights, joints, and contact forces of each object. This project uses rigid body simulation to model the motion of the device, with the objective to inform designers on how the device will move. By using established simulation software, it is easier to model the device using fewer assumptions than in the maths model, leading to a more accurate system.\\
\\
\section{Selection of simulator}
The simulation programs considered in this project are PyBullet, Gazebo, and Drake. Each of these have their own advantages but Drake was selected due to its focus on accurate multibody and friction simulation \citep{drake}.
\\
Drake is a multibody physics engine developed and used by MIT. This project uses Drake's python bindings which are available in the package "pydrake", which runs on Ubuntu using Windows Subsystem for Linux (WSL).\\
\section{CAD to simulation pipeline}
To model a robot, Drake requires a simulation description format file (SDFormat). Currently, not many CAD programs provide a method to easily generate these files. This project used Onshape, a cloud-based CAD program, for this reason. The python library, "onshape-to-robot" \citep{converter}, is then used to build an SDFormat file. The generated SDFormat file is then modified in order to meet Drake's specific requirements, and to apply realistic coefficients of friction to the wheels and tail.\\

\section{Using the simulator}
Once the robot has been loaded into the multibody simulation, it can be driven by setting a torque on the motor joints. Simply setting the torque on the joint to a constant value would cause the device to accelerate continuously ad infinitum. DC motor torque decreases as the speed increases until the torque reaches an equilibrium with the resistive forces and a constant speed is achieved. Equation \ref{eq:torqueVoltageSpeed} models the toque output of a geared DC motor.\\

\begin{equation}
	T_\mathrm{Stall} = T_\mathrm{Rated-stall}\frac{V_\mathrm{Terminal}}{V_\mathrm{Rated}} 
	\label{eq:torqueVoltageSpeed}
\end{equation}
This essentially acts as a high-gain proportional speed controller. The motor voltage is set through sliders in the simulator options. \\
The device can now be tested in simulation to determine whether it can climb stairs, and to gain insight into which components make contact with the stairs and when. Figure \ref{fig:simulation-screenshot} shows the device climbing a set of stairs in the Drake simulator.\\

\begin{figure}[h]
	\centering
	
	\caption{Screenshot of the device climbing steps in the Drake simulation.}
	\label{fig:simulation-screenshot}
\end{figure}

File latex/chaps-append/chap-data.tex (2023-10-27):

\chapter{Data} \label{app:data}

\begin{table}[!ht]
	\centering
	\caption{Required torque (Nm) for each stage of motion from the model, simulation, and experiment.}
	\footnotesize
	\begin{tabular}{|l|l|l|l|l|l|l|l|l|l|}
		\hline
		Stage & ~ & ~ & ~ & ~ & ~ & ~ & ~ & ~ & ~ \\ \hline
		~ & ~ & 1 & 1 & 3 & 3 & 4 & 4 & 6 & 6 \\ \hline
		~ & ~ & partial & full & partial & full & partial & full & partial & full \\ \hline
		default & Model & 0.52 & 0.52 & 0.31 & 0.52 & 0.67 & 0.77 & 0.35 & 0.69 \\ \hline
		~ & Simulation & 0.53 & 0.68 & 0.41 & 0.48 & 0.54 & 0.84 & 0.47 & 0.59 \\ \hline
		~ & Experiment & 0.62 & 0.73 & 0.39 & 0.39 & 0.78 & 0.89 & 0.62 & 0.78 \\ \hline
		60cm tail & model & 0.58 & 0.58 & 0.33 & 0.58 & 0.7 & 0.75 & 0.38 & 0.77 \\ \hline
		~ & simulation & 0.71 & 0.8 & 0.56 & 0.56 & 0.8 & 0.85 & 0.48 & 0.6 \\ \hline
		~ & experiment & 0.71 & 0.75 & 0.39 & 0.48 & 0.78 & 0.95 & 0.61 & 0.78 \\ \hline
		343g mass & model & 0.62 & 0.62 & 0.37 & 0.62 & 0.85 & 1.13 & 0.45 & 0.99 \\ \hline
		~ & simulation & 0.67 & 0.87 & 0.52 & 0.6 & 0.71 & 1.07 & 0.63 & 0.7 \\ \hline
		~ & experiment & 0.84 & 0.89 & 0.47 & 0.53 & 0.9 & 1.26 & 0.65 & 0.91 \\ \hline
	\end{tabular}
\end{table}
\begin{landscape}

\begin{table}[!ht]
	\centering
	\caption{Voltage, assessment, and calculated torque for Stage 1 motion.}
	\footnotesize
	\begin{tabular}{|l|l|l|l|l|l|l|l|l|}
		\hline
		Default device & ~ & ~ & 60 cm tail & ~ & ~ & 340g added weight & ~ & ~ \\ \hline
		Voltage (V) & Assessment & Torque (Nm) & Voltage (V) & Assessment & Torque (Nm) & Voltage (V) & Assessment & Torque (Nm) \\ \hline
		0.89 & 0 & 0.099974 & 1.58 & 0 & 0.456428 & 2.58 & 1 & 0.973028 \\ \hline
		1.08 & 0 & 0.198128 & 1.95 & 0 & 0.64757 & 2.78 & 1 & 1.076348 \\ \hline
		1.12 & 0 & 0.218792 & 2.04 & 0 & 0.694064 & 2.42 & 1 & 0.890372 \\ \hline
		1.57 & 0 & 0.451262 & 2.65 & 1 & 1.00919 & 1.99 & 0 & 0.668234 \\ \hline
		1.68 & 0 & 0.508088 & 2.41 & 1 & 0.885206 & 1.77 & 0 & 0.554582 \\ \hline
		1.74 & 0 & 0.539084 & 2.24 & 1 & 0.797384 & 2.06 & 0 & 0.704396 \\ \hline
		1.81 & 0 & 0.575246 & 2.16 & 1 & 0.756056 & 2.15 & 0 & 0.75089 \\ \hline
		1.87 & 0 & 0.606242 & 2.08 & 0.5 & 0.714728 & 2.2 & 0 & 0.77672 \\ \hline
		1.89 & 0.5 & 0.616574 & 2.03 & 0 & 0.688898 & 2.44 & 1 & 0.900704 \\ \hline
		1.98 & 0.5 & 0.663068 & 2.09 & 0.5 & 0.719894 & 2.31 & 0.5 & 0.833546 \\ \hline
		2.05 & 0.5 & 0.69923 & 2.14 & 0.5 & 0.745724 & 2.32 & 0.5 & 0.838712 \\ \hline
		2.11 & 1 & 0.730226 & 2.28 & 1 & 0.818048 & 2.49 & 1 & 0.926534 \\ \hline
		2.13 & 1 & 0.740558 & ~ & ~ & ~ & ~ & ~ & ~ \\ \hline
		2.25 & 1 & 0.80255 & ~ & ~ & ~ & ~ & ~ & ~ \\ \hline
		2.26 & 1 & 0.807716 & ~ & ~ & ~ & ~ & ~ & ~ \\ \hline
		2.3 & 1 & 0.82838   & ~ & ~ & ~ & ~ & ~ & ~ \\ \hline
	\end{tabular}
\end{table}

\begin{table}[!ht]
	\centering
	\caption{Voltage, assessment, and calculated torque for Stage 3 motion.}
	\footnotesize
	\begin{tabular}{|l|l|l|l|l|l|l|l|l|}
		\hline
		Default device & ~ & ~ & 60 cm tail & ~ & ~ & 340g added weight & ~ & ~ \\ \hline
		Voltage (V) & Assessment & Torque (Nm) & Voltage (V) & Assessment & Torque (Nm) & Voltage (V) & Assessment & Torque (Nm) \\ \hline
		2.25 & 1 & 0.80255 & 2.65 & 1 & 1.00919 & 2.35 & 1 & 0.85421 \\ \hline
		1.73 & 1 & 0.533918 & 2.56 & 1 & 0.962696 & 2.3 & 1 & 0.82838 \\ \hline
		1.45 & 1 & 0.38927 & 2.06 & 1 & 0.704396 & 2.03 & 1 & 0.688898 \\ \hline
		1.49 & 1 & 0.409934 & 1.61 & 1 & 0.471926 & 1.75 & 1 & 0.54425 \\ \hline
		0.66 & 0 & -0.018844 & 1.45 & 0.5 & 0.38927 & 1.64 & 0.5 & 0.487424 \\ \hline
		0.81 & 0 & 0.058646 & 1.22 & 0 & 0.270452 & 1.69 & 0.5 & 0.513254 \\ \hline
		0.99 & 0 & 0.151634 & 1.06 & 0 & 0.187796 & 1.73 & 1 & 0.533918 \\ \hline
		1.07 & 0 & 0.192962 & 1.39 & 0 & 0.358274 & 1.5 & 0 & 0.4151 \\ \hline
		1.25 & 0 & 0.28595 & 1.42 & 0 & 0.373772 & 1.41 & 0 & 0.368606 \\ \hline
		1.3 & 0 & 0.31178 & 1.45 & 0 & 0.38927 & 1.56 & 0 & 0.446096 \\ \hline
		1.34 & 0 & 0.332444 & 1.41 & 0 & 0.368606 & 1.58 & 0 & 0.456428 \\ \hline
		1.42 & 0 & 0.373772 & 1.52 & 0.5 & 0.425432 & 1.61 & 0.5 & 0.471926 \\ \hline
		1.49 & 1 & 0.409934 & 1.63 & 1 & 0.482258 & ~ & ~ & ~ \\ \hline
		~ & ~ & ~ & 1.72 & 1 & 0.528752 & ~ & ~ & ~ \\ \hline
		~ & ~ & ~ & 1.67 & 1 & 0.502922 & ~ & ~ & ~ \\ \hline
		~ & ~ & ~ & 1.49 & 0 & 0.409934 & ~ & ~ & ~ \\ \hline
		~ & ~ & ~ & 1.56 & 0.5 & 0.446096 & ~ & ~ & ~ \\ \hline
	\end{tabular}
\end{table}

\begin{table}[!ht]
	\centering
	\caption{Voltage, assessment, and calculated torque for Stage 4 motion.}
	\footnotesize
	\begin{tabular}{|l|l|l|l|l|l|l|l|l|}
		\hline
		Default device & ~ & ~ & 60 cm tail & ~ & ~ & 340g added weight & ~ & ~ \\ \hline
		Voltage (V) & Assessment & Torque (Nm) & Voltage (V) & Assessment & Torque (Nm) & Voltage (V) & Assessment & Torque (Nm) \\ \hline
		2.61 & 1 & 0.988526 & 1.68 & 0 & 0.508088 & 1.58 & 0 & 0.456428 \\ \hline
		2.91 & 1 & 1.143506 & 2.81 & 1 & 1.091846 & 1.84 & 0 & 0.590744 \\ \hline
		2.99 & 1 & 1.184834 & 2.79 & 1 & 1.081514 & 2.07 & 0 & 0.709562 \\ \hline
		2.83 & 1 & 1.102178 & 2.42 & 0.5 & 0.890372 & 2.38 & 0 & 0.869708 \\ \hline
		2.78 & 1 & 1.076348 & 2.21 & 0 & 0.781886 & 2.66 & 0.5 & 1.014356 \\ \hline
		2.65 & 1 & 1.00919 & 2.04 & 0 & 0.694064 & 2.61 & 0.5 & 0.988526 \\ \hline
		2.56 & 1 & 0.962696 & 1.73 & 0 & 0.533918 & 2.48 & 0.5 & 0.921368 \\ \hline
		2.48 & 1 & 0.921368 & 1.93 & 0 & 0.637238 & 2.47 & 0.5 & 0.916202 \\ \hline
		2.43 & 1 & 0.895538 & 2.26 & 0.5 & 0.807716 & 2.45 & 0.5 & 0.90587 \\ \hline
		2.28 & 0.5 & 0.818048 & 2.32 & 0.5 & 0.838712 & 2.42 & 0.5 & 0.890372 \\ \hline
		2.38 & 0.5 & 0.869708 & 2.15 & 0 & 0.75089 & 2.2 & 0 & 0.77672 \\ \hline
		2.3 & 0.5 & 0.82838 & 2.22 & 0 & 0.787052 & 2.27 & 0 & 0.812882 \\ \hline
		2.22 & 0.5 & 0.787052 & 2.36 & 0.5 & 0.859376 & 2.43 & 0.5 & 0.895538 \\ \hline
		2.08 & 0 & 0.714728 & 2.62 & 1 & 0.993692 & 2.66 & 0.5 & 1.014356 \\ \hline
		2 & 0 & 0.6734 & 2.63 & 1 & 0.998858 & 2.93 & 0.5 & 1.153838 \\ \hline
		2.12 & 0 & 0.735392 & 2.53 & 1 & 0.947198 & 3.18 & 1 & 1.282988 \\ \hline
		2.16 & 0 & 0.756056 & 2.25 & 0.5 & 0.80255 & 3.04 & 0.5 & 1.210664 \\ \hline
		~ & ~ & ~ & 2.22 & 0.5 & 0.787052 & 3.1 & 0.5 & 1.24166 \\ \hline
		~ & ~ & ~ & 2.6 & 1 & 0.98336 & 3.34 & 1 & 1.365644 \\ \hline
		~ & ~ & ~ & ~ & ~ & ~ & 3.14 & 1 & 1.262324 \\ \hline
	\end{tabular}
\end{table}

\begin{table}[!ht]
	\centering
	\caption{Voltage, assessment, and calculated torque for Stage 6 motion.}
	\footnotesize
	\begin{tabular}{|l|l|l|l|l|l|l|l|l|}
		\hline
		Default device & ~ & ~ & 60 cm tail & ~ & ~ & 340g added weight & ~ & ~ \\ \hline
		Voltage (V) & Assessment & Torque (Nm) & Voltage (V) & Assessment & Torque (Nm) & Voltage (V) & Assessment & Torque (Nm) \\ \hline
		1.52 & 0 & 0.425432 & 1.91 & 0.5 & 0.626906 & 3.42 & 1 & 1.406972 \\ \hline
		1.68 & 0 & 0.508088 & 1.78 & 0 & 0.559748 & 2.81 & 1 & 1.091846 \\ \hline
		1.91 & 0.5 & 0.626906 & 1.83 & 0 & 0.585578 & 2.05 & 0.5 & 0.69923 \\ \hline
		2.12 & 0.5 & 0.735392 & 1.87 & 0.5 & 0.606242 & 2.09 & 0.5 & 0.719894 \\ \hline
		2.45 & 1 & 0.90587 & 1.95 & 0.5 & 0.64757 & 2.15 & 0.5 & 0.75089 \\ \hline
		2.22 & 1 & 0.787052 & 2.13 & 0.5 & 0.740558 & 2.12 & 0.5 & 0.735392 \\ \hline
		2.33 & 1 & 0.843878 & 2.27 & 1 & 0.812882 & 2.3 & 0.5 & 0.82838 \\ \hline
		2.08 & 0.5 & 0.714728 & 2.23 & 1 & 0.792218 & 2.46 & 1 & 0.911036 \\ \hline
		2.1 & 0.5 & 0.72506 & 2.2 & 1 & 0.77672 & 2.43 & 0.5 & 0.895538 \\ \hline
		2.2 & 1 & 0.77672 & 2.17 & 0.5 & 0.761222 & 2.41 & 0.5 & 0.885206 \\ \hline
		1.6 & 0 & 0.46676 & 2.23 & 1 & 0.792218 & 2.46 & 0.5 & 0.911036 \\ \hline
		1.92 & 0.5 & 0.632072 & ~ & ~ & ~ & 2.48 & 1 & 0.921368 \\ \hline
		1.84 & 0 & 0.590744 & ~ & ~ & ~ & 2.7 & 1 & 1.03502 \\ \hline
		1.91 & 0.5 & 0.626906 & ~ & ~ & ~ & 2.79 & 1 & 1.081514 \\ \hline
		~ & ~ & ~ & ~ & ~ & ~ & 2.65 & 1 & 1.00919 \\ \hline
		~ & ~ & ~ & ~ & ~ & ~ & 1.95 & 0.5 & 0.64757 \\ \hline
		~ & ~ & ~ & ~ & ~ & ~ & 1.92 & 0 & 0.632072 \\ \hline
	\end{tabular}
\end{table}

\end{landscape}

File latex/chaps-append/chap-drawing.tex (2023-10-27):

\chapter{Engineering drawings and parts list}

This appendix contains the engineering drawings of the LIM device. The .dxf files of the parts to be laser cut can be found in Drawing-files/v2/ in the project repository \citep{repo}.
%\afterpage{
%\KOMAoptions{paper=A3,paper=landscape,pagesize}
%\recalctypearea

\includepdf[pages=-, fitpaper]{chaps-append/STAIR-CLIMBER.pdf}

%\clearpage%\KOMAoptions{paper=A4,paper=portrait, pagesize}
%\recalctypearea

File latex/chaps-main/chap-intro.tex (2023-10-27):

\chapter{Introduction}

\section{Background}

During disasters such as earthquakes, Urban Search And Rescue (USAR) robots are used to detect victims in hazardous environments where first responders would otherwise be put at risk. Advanced USAR robots can explore and map the environment while overcoming obstacles, and deliver supplies to victims who cannot be immediately evacuated. USAR robots were first used in the aftermath of the September 11 attacks on the World Trade Centre, where they had limited success as they would frequently get stuck or damaged. Since then, designs for USAR robots with many different locomotion methods have been considered and compared in competitions such as the RoboCup Rescue Robot League and the DARPA Robotics Challenge. At present, USAR robots are typically only successful at surveillance; due to the extreme conditions in disaster zones and the urgency of rescue operations, first responders will rarely consider using USAR robots.\\

\begin{wrapfigure}{r}{0.35\textwidth} %this figure will be at the right
	\centering
	
	\caption{Systems layout of Wilson's LIM device \citep{Wilson-2013}.}
	\label{Wilson sketch}
\end{wrapfigure}

\noindent Another problem limiting the use of USAR robots is cost; USAR robots are prohibitively expensive so rescue organisations use them sparingly. There is a need for low-cost, expendable USAR robots. In 2013, Matthew Wilson proposed an automatically-shape-shifting platform that uses a Load Intuitive Module (LIM) in the place of regular wheels, shown in Figure \ref{Wilson sketch} \citep{Wilson-2013}. The LIM system uses two outer "minor wheels" placed on a central hub that can be rotated as a "major wheel". The minor wheels are geared to the central hub such that they drive the vehicle, however if they experience high resistance, for example from hitting an obstacle, the torque will cause the major wheel to rotate instead, flipping one of the minor wheels over the obstacle to automatically climb it. This is a strong concept for an inexpensive stair-climbing robot as it only uses a single motor for both normal driving and climbing obstacles.\\

\noindent "LIMed" robot platforms (platforms using LIMs for locomotion) were built individually by four final year students at UCT \citep{Wilson-2013},  \citep{Haskel-2017}, \citep{Buchanan-2018}, and \citep{Powrie-2019}. One of these robots is shown in Figure \ref{Powrie robot}. These platforms show some success in climbing a single step, albeit inconsistently. Powrie noted that a mathematical model that accurately describes the kinematics of the system could be developed to optimise the design of LIMed robots. This project is a continuation of these students' work.

\begin{figure}[h]
	\centering
	
	\caption{Powrie's "Di-Wheel" robot \citep{Powrie-2019}.}
	\label{Powrie robot}
\end{figure}

\section{Objectives}
The aim of this project is to create a model that can be used to inform future USAR designs.
The following objectives were identified to meet this aim:
\begin{enumerate}
	\item Create a model to describe the kinematics of a LIM.
	\item Build a prototype USAR device which uses LIMs to climb stairs.
	\item Validate the model using the prototype.
\end{enumerate}
This project does not intend to create a fully functioning USAR robot, but rather a prototype of the platform that a USAR robot may use.
\section{Motivation}

Many designs for USAR locomotion exist, however highly capable devices are prohibitively expensive. There remains a need for USAR devices that are both affordable and effective, and LIMed USAR robots could fill that role in the near future. Designers will be able to use the model produced in this report to design and optimise LIMed USAR robots. These robots use fewer actuators so could be cheaper than existing USAR robots. Lowering the cost of USAR robots is a priority as it makes them more accessible to rescue organisations.

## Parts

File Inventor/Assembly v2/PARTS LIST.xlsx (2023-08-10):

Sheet: Parts List External
ITEM | DESCRIPTION | QTY | MATERIAL -SPECIFICATIONS | PART NUMBER | FROM WHERE | READY TO ORDER? | DATE EXPECTED | STATUS | HAVE IT? | ANY PROBLEMS | IDENTICAL?
4 | JGY-370Output Shaft | 2 |  |  | COMMUNICA |  |  |  | X |  | X
14 | JGY-37012V DC Motor | 2 |  |  | COMMUNICA |  |  |  | X |  | X
21 | JGY-370Gearbox | 2 |  |  | COMMUNICA |  |  |  | X |  | X
1 | M5-washer | 28 |  |  | HARDWARE STORE | X |  |  |  |  | X
6 | 6mm D SHAFT | 4 | STEEL | M001 | HARDWARE STORE |  | 2023-08-04 | ordered |  |  | X
7 | Tail | 1 |  |  | HARDWARE STORE |  |  |  | X |  | X
9 | 5m hex nut | 12 |  |  | HARDWARE STORE |  |  |  | X |  | X
11 | M5 BOLT FLATTENED | 4 | STEEL | M002 | HARDWARE STORE |  | 2023-08-04 | ordered |  |  | X
16 | m5-bolt-long | 3 |  |  | HARDWARE STORE |  |  |  | X |  | X
17 | m3 bolt | 8 |  |  | HARDWARE STORE |  |  |  | X |  | X
18 | M5-nut-4mm | 3 |  |  | HARDWARE STORE |  |  |  | X |  | X
22 | M3-nut | 12 |  |  | HARDWARE STORE |  |  |  | X |  | X
23 | m3 bolt long | 12 |  |  | HARDWARE STORE |  |  |  | X |  | X
2 | SHAFT EXTENSION | 2 | STEEL | M003 | Micro robotics |  | 2023-08-04 | ordered coupling |  |  | X
3 | Sun gear | 4 | ACRYLIC |  | NETRAM |  | 2023-08-04 | ordered |  |  | X
5 | Idler Gear | 8 | ACRYLIC |  | NETRAM |  | 2023-08-04 | ordered |  |  | X
8 | tail fin | 4 | MDF |  | NETRAM |  | 2023-08-04 | ordered |  |  | X
10 | Spur Gear22 | 8 | ACRYLIC |  | NETRAM |  | 2023-08-04 | ordered |  |  | X
12 | Wheel | 4 | MDF |  | NETRAM |  | 2023-08-04 | ordered |  |  | X
13 | bottom plate | 2 | MDF |  | NETRAM |  | 2023-08-04 | ordered |  |  | X
15 | side plate | 2 | MDF |  | NETRAM |  | 2023-08-04 | ordered |  |  | X
19 | Back Plate | 1 | MDF |  | NETRAM |  | 2023-08-04 | ordered |  |  | X
20 | front plate | 1 | MDF |  | NETRAM |  | 2023-08-04 | ordered |  |  | X
24 | Frame | 4 | ACRYLIC |  | NETRAM |  | 2023-08-04 | ordered |  |  | X
25 | Standoff-thin | 24 | ACRYLIC |  | NETRAM |  | 2023-08-04 | ordered |  |  | X
26 | Standoff-thick | 12 | ACRYLIC |  | NETRAM |  | 2023-08-04 | ordered |  |  | X

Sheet: Parts List University
ITEM | DESCRIPTION | QTY | MATERIAL -SPECIFICATIONS | PART NUMBER | FROM WHERE | READY TO ORDER? | STATUS | HAVE IT? | ANY PROBLEMS | IDENTICAL?
4 | JGY-370Output Shaft | 2 |  |  | COMMUNICA | X |  |  |  | X
14 | JGY-37012V DC Motor | 2 |  |  | COMMUNICA | X |  |  |  | X
21 | JGY-370Gearbox | 2 |  |  | COMMUNICA | X |  |  |  | X
1 | M5-washer | 28 |  |  | HARDWARE STORE |  |  | X |  | X
7 | Tail | 1 |  |  | HARDWARE STORE |  |  | X |  | X
9 | 5m hex nut | 12 |  |  | HARDWARE STORE |  |  | X |  | X
16 | m5-bolt-long | 3 |  |  | HARDWARE STORE |  |  | X |  | X
17 | m3 bolt | 8 |  |  | HARDWARE STORE |  |  | X |  | X
18 | M5-nut-4mm | 3 |  |  | HARDWARE STORE |  |  | X |  | X
22 | M3-nut | 12 |  |  | HARDWARE STORE |  |  | X |  | X
23 | m3 bolt long | 12 |  |  | HARDWARE STORE |  |  | X |  | X
3 | Sun gear | 4 | ACRYLIC |  | UNIVERSITY LASER CUT |  | purchasing material |  |  | X
5 | Idler Gear | 8 | ACRYLIC |  | UNIVERSITY LASER CUT |  | purchasing material |  |  | X
8 | tail fin | 4 | MDF |  | UNIVERSITY LASER CUT | X |  |  |  | X
10 | Spur Gear22 | 8 | ACRYLIC |  | UNIVERSITY LASER CUT |  | purchasing material |  |  | X
12 | Wheel | 4 | MDF |  | UNIVERSITY LASER CUT | X |  |  |  | X
13 | bottom plate | 2 | MDF |  | UNIVERSITY LASER CUT | X |  |  |  | X
15 | side plate | 2 | MDF |  | UNIVERSITY LASER CUT | X |  |  |  | X
19 | Back Plate | 1 | MDF |  | UNIVERSITY LASER CUT | X |  |  |  | X
20 | front plate | 1 | MDF |  | UNIVERSITY LASER CUT | X |  |  |  | X
24 | Frame | 4 | ACRYLIC |  | UNIVERSITY LASER CUT |  | purchasing material |  |  | X
25 | Standoff-thin | 24 | ACRYLIC |  | UNIVERSITY LASER CUT |  | purchasing material |  |  | X
26 | Standoff-thick | 12 | ACRYLIC |  | UNIVERSITY LASER CUT |  | purchasing material |  |  | X
2 | SHAFT EXTENSION | 2 | STEEL | M003 | UNIVERSITY MMW |  | in queue |  |  | X
6 | 6mm D SHAFT | 4 | STEEL | M001 | UNIVERSITY MMW |  | in queue |  |  | X
11 | M5 BOLT FLATTENED | 4 | STEEL | M002 | UNIVERSITY MMW |  | in queue |  |  | X

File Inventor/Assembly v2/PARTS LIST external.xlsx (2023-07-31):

ITEM | DESCRIPTION | QTY | MATERIAL -SPECIFICATIONS | PART NUMBER | FROM WHERE | READY TO ORDER? | STATUS | HAVE IT? | ANY PROBLEMS | IDENTICAL?
1 | M5-washer | 28 |  |  | HARDWARE STORE |  |  | X |  | X
2 | SHAFT EXTENSION | 2 | STEEL | M003 | EXTERNAL MACHINE WORKSHOP |  |  |  | must get quotes | X
3 | Sun gear | 4 | ACRYLIC |  | NETRAM | X |  |  |  | X
4 | JGY-370Output Shaft | 2 |  |  | COMMUNICA |  |  | X |  | X
5 | Idler Gear | 8 | ACRYLIC |  | NETRAM | X |  |  |  | X
6 | 6mm D SHAFT | 4 | STEEL | M001 | EXTERNAL MACHINE WORKSHOP |  |  |  | must get quotes | X
7 | Tail | 1 |  |  | HARDWARE STORE |  |  | X |  | X
8 | tail fin | 4 | MDF |  | NETRAM | X |  |  |  | X
9 | 5m hex nut | 12 |  |  | HARDWARE STORE |  |  | X |  | X
10 | Spur Gear22 | 8 | ACRYLIC |  | NETRAM | X |  |  |  | X
11 | M5 BOLT FLATTENED | 4 | STEEL | M002 | EXTERNAL MACHINE WORKSHOP |  |  |  | must get quotes | X
12 | Wheel | 4 | MDF |  | NETRAM | X |  |  |  | X
13 | bottom plate | 2 | MDF |  | NETRAM | X |  |  |  | X
14 | JGY-37012V DC Motor | 2 |  |  | COMMUNICA |  |  | X |  | X
15 | side plate | 2 | MDF |  | NETRAM | X |  |  |  | X
16 | m5-bolt-long | 3 |  |  | HARDWARE STORE |  |  | X |  | X
17 | m3 bolt | 8 |  |  | HARDWARE STORE |  |  | X |  | X
18 | M5-nut-4mm | 3 |  |  | HARDWARE STORE |  |  | X |  | X
19 | Back Plate | 1 | MDF |  | NETRAM | X |  |  |  | X
20 | front plate | 1 | MDF |  | NETRAM | X |  |  |  | X
21 | JGY-370Gearbox | 2 |  |  | COMMUNICA |  |  | X |  | X
22 | M3-nut | 12 |  |  | HARDWARE STORE |  |  | X |  | X
23 | m3 bolt long | 12 |  |  | HARDWARE STORE |  |  | X |  | X
24 | Frame | 4 | ACRYLIC |  | NETRAM | X |  |  |  | X
25 | Standoff-thin | 24 | ACRYLIC |  | NETRAM | X |  |  |  | X
26 | Standoff-thick | 12 | ACRYLIC |  | NETRAM | X |  |  |  | X

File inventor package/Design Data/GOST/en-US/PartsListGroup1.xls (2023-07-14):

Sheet: Лист 1
Инв. № подл |  |  |  | Подп. и дата | Взам. инв. № | Инв. № дубл. |  |  | Подп. и дата
Формат | Зона | Поз. | Обозначение |  |  |  | Наименование |  |  |  |  |  | Кол. на исполнение
 |  |  |  |  |  |  |  |  |  |  |  | Лит.
 |  |  |  |  |  |  |  |  |  |  |  | Код
 |  |  |  |  |  |  |  | Изм. | Лист | № докум | Подпись |  | Дата
 |  |  |  |  |  |  |  | Разраб.
 |  |  |  |  |  |  |  | Пров.
 |  |  |  |  |  |  |  | Н.контр
 |  |  |  |  |  |  |  | Утв.
 |  |  |  |  |  |  |  |  |  |  |  |  |  | Копировал

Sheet: Лист 2
Инв. № подл |  |  |  | Подп. и дата | Взам. инв. № | Инв. № дубл. |  |  | Подп. и дата
Формат | Зона | Поз. | Обозначение |  |  |  | Наименование |  |  |  |  | Кол. на исполнение
 |  |  |  |  |  |  |  | Изм. | Лист | № докум. | Подп. | Дата
 |  |  |  |  |  |  |  |  |  |  |  |  | Копировал
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

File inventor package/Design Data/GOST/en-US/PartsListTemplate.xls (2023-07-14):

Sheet: Лист 1
 | Формат | Зона |  | Поз. |  | Обозначение |  |  |  | Наименование |  |  |  | Кол. | Приме-чание
Подп. и дата
Инв. № дубл.
Взам. инв. №
Подп. и дата
 | Изм. |  | Лист |  | № докум |  | Подпись | Дата
Инв. № подл | Разраб. |  |  |  |  |  |  |  |  |  | Литера |  | Лист |  |  | Листов
 | Пров.
 | Н.контр
 | Утв.
 |  |  |  |  |  |  |  |  | Копировал |  |  | Формат А4

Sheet: Лист 2
 | Формат | Зона |  | Поз. |  | Обозначение |  |  |  | Наименование |  | Кол. | Приме-чание
Подп. и дата
Инв. № дубл.
Взам. инв. №
Подп. и дата
Инв. № подл
 | Изм. |  | Лист |  | № докум. |  | Подп. |  | Дата
 |  |  |  |  |  |  |  | Копировал |  |  | Формат А4
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

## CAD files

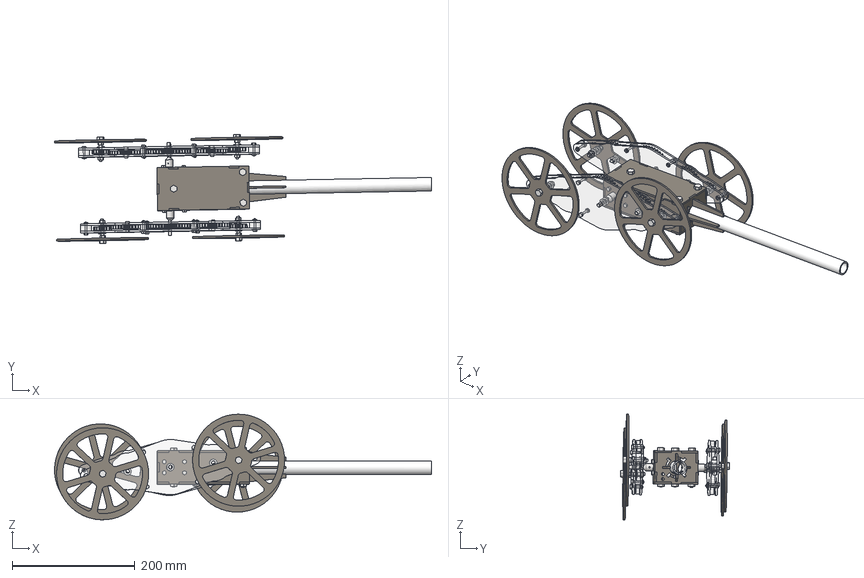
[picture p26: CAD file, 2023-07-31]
Inventor/Assembly v2/Assembly.step
614.4 x 177.6 x 172.2 mm
M5-washer x 28
Shaft extension x 2
Sun gear x 4
JGY-370Output Shaft x 2
Idler Gear x 8
Shaft2 x 4
Tail
tail fin x 4
5m hex nut x 12
Spur Gear22 x 8
m5-screw-cut x 4
Wheel x 4
bottom plate x 2
JGY-37012V DC Motor x 2
side plate x 2
m5-bolt-long x 3
m3 bolt x 8
M5-nut-4mm x 3
Back Plate
front plate
JGY-370Gearbox x 2
M3-nut x 12
m3 bolt long x 12
Frame x 4
Standoff-thin x 24
Standoff-thick x 12

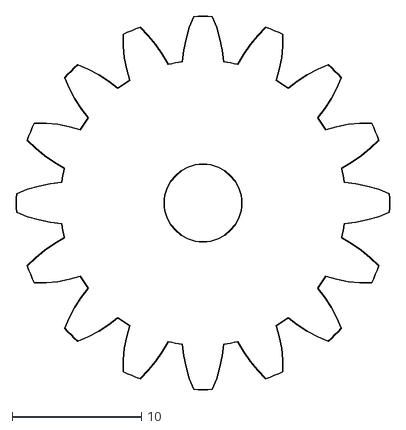
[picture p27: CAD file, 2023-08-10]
Drawing-files/v2/8x - PLANET GEAR ALTERNATE - 3mm Acrylic.dxf
28.8 x 28.8

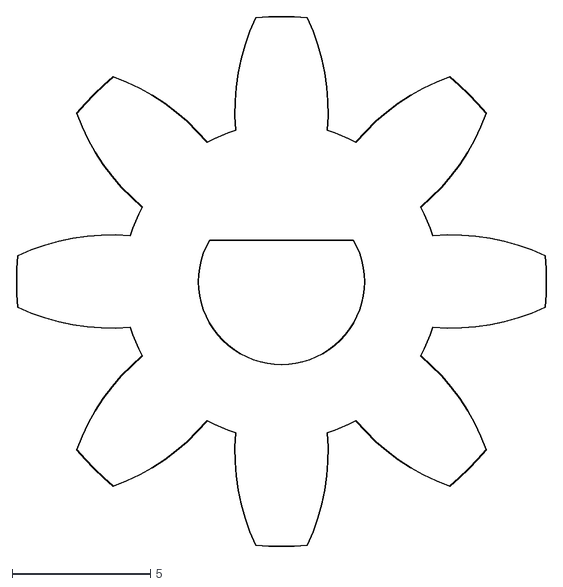
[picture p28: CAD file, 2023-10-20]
Drawing-files/v3 - New gears/8x - PLANET GEAR - 3mm Acrylic.dxf
19.2 x 19.2

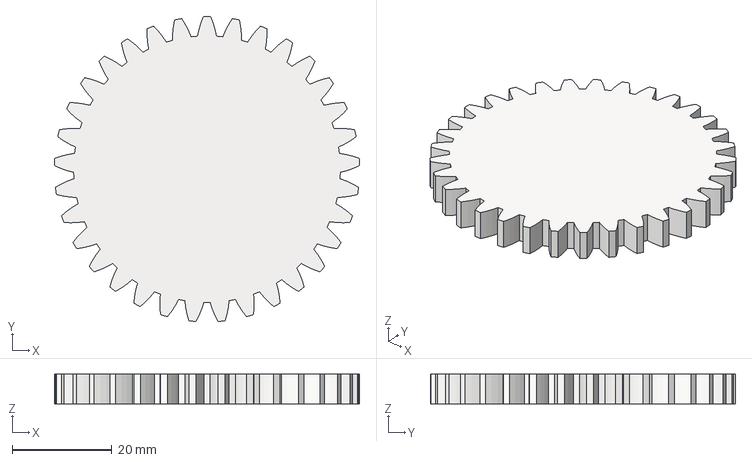
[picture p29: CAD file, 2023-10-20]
Inventor/New_idler.stp
61.1 x 61.0 x 6.00 mm

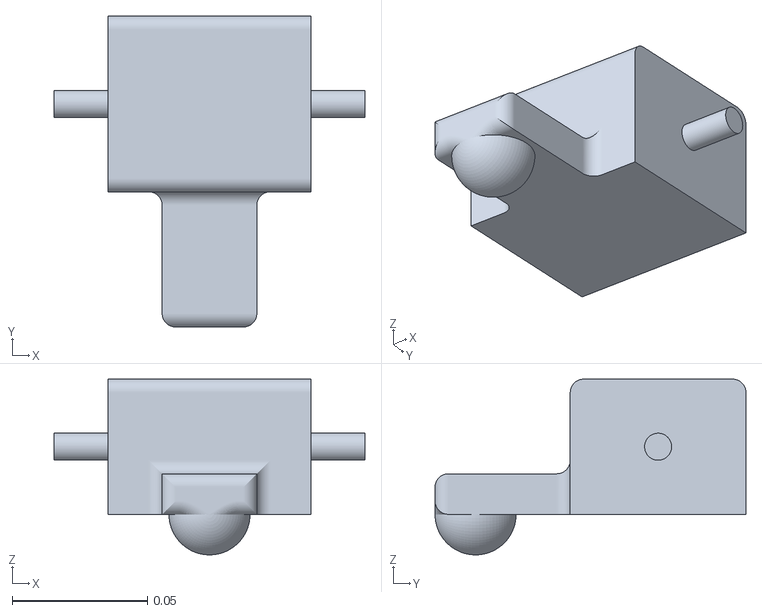
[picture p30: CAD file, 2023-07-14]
vscode/2wheels/body.stl
0.115 x 0.115 x 0.065

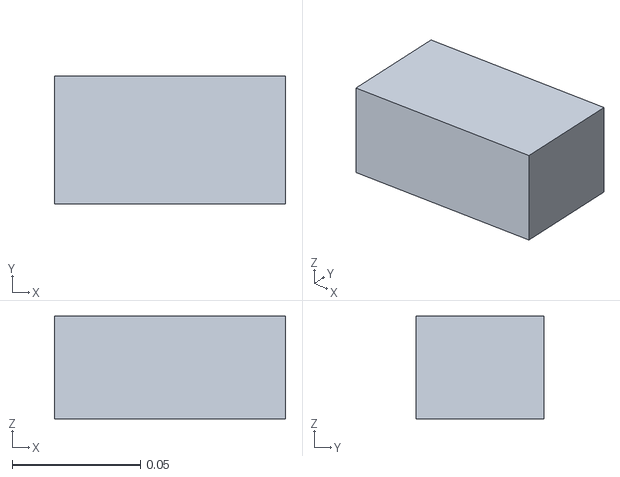
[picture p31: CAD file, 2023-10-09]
vscode/my-robot-addedWeight/mass.stl
0.09 x 0.05 x 0.04

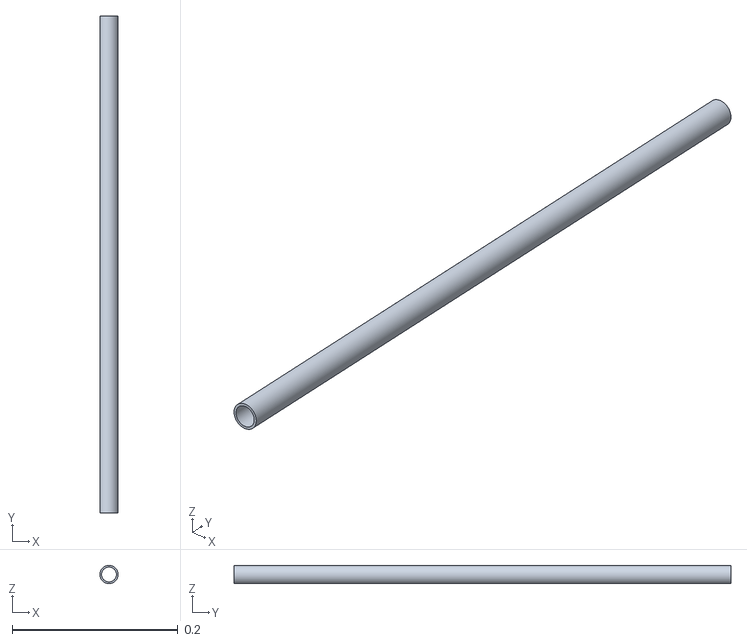
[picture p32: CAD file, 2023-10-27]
vscode/my-robot-longTail/tail.stl
0.022 x 0.6 x 0.022

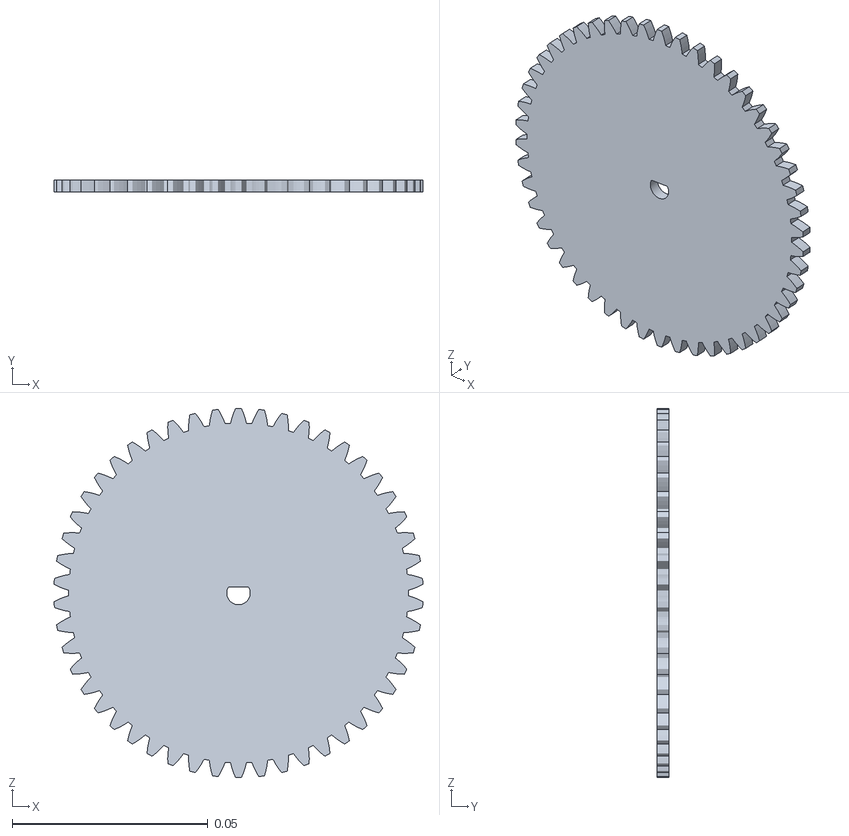
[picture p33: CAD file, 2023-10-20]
vscode/my-robot-newGears/spur_gear27.stl
0.0942 x 0.003 x 0.0943

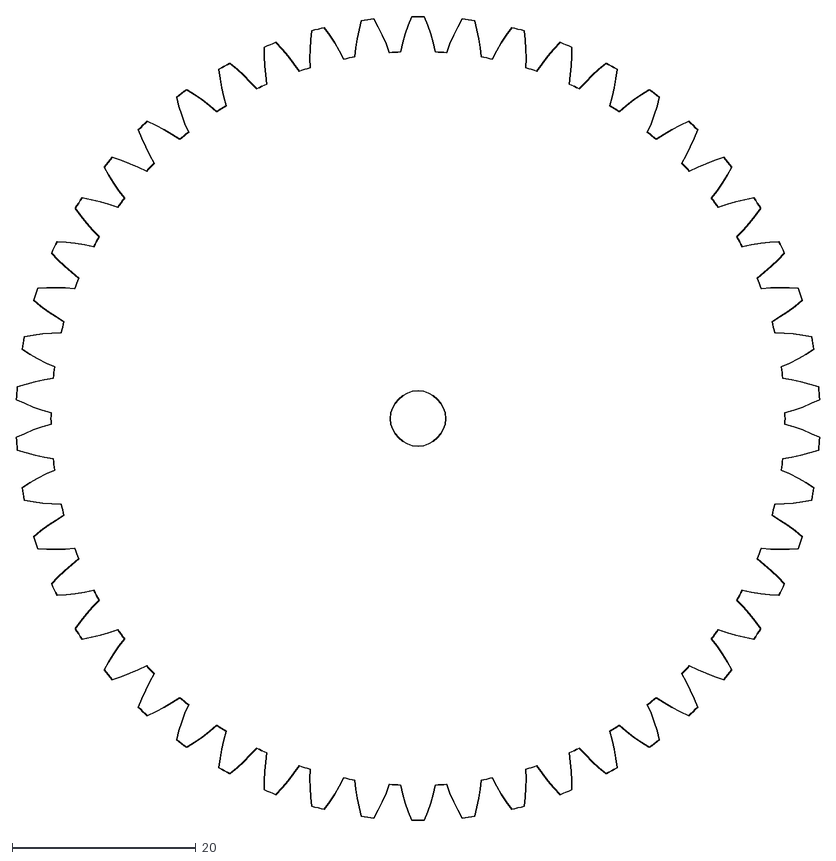
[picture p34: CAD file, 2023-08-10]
Drawing-files/v2/4x - SUN GEAR ALTERNATE - 3mm Acrylic.dxf
87.4 x 87.5

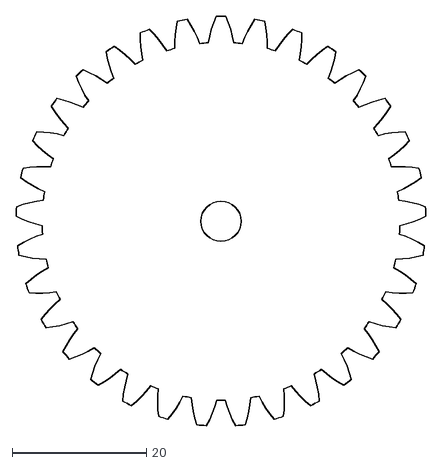
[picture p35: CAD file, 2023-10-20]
Drawing-files/v3 - New gears/8x - IDLER GEAR - 3mm Acrylic.dxf
61.1 x 61.0

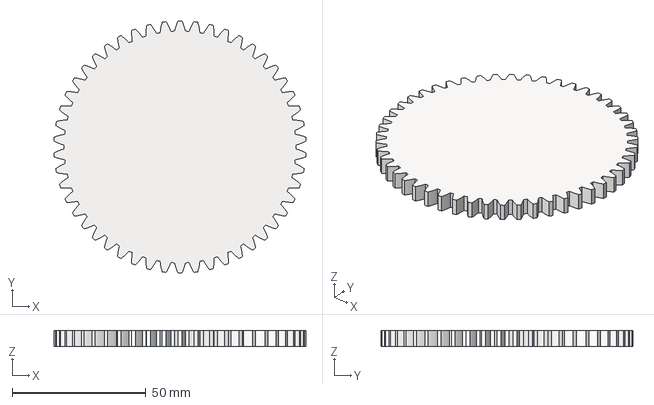
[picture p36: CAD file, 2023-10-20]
Inventor/New_sun.stp
94.2 x 94.3 x 6.00 mm

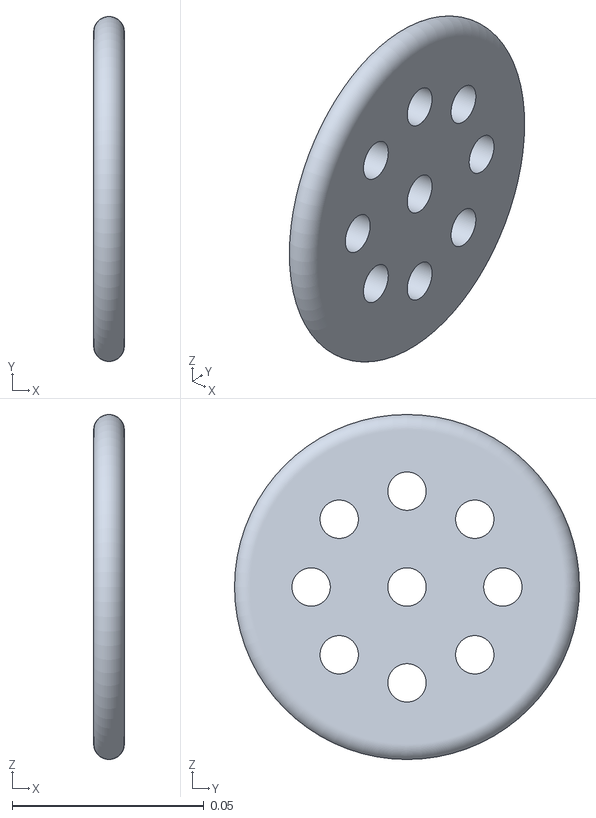
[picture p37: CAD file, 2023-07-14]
vscode/2wheels/wheel.stl
0.008 x 0.09 x 0.09

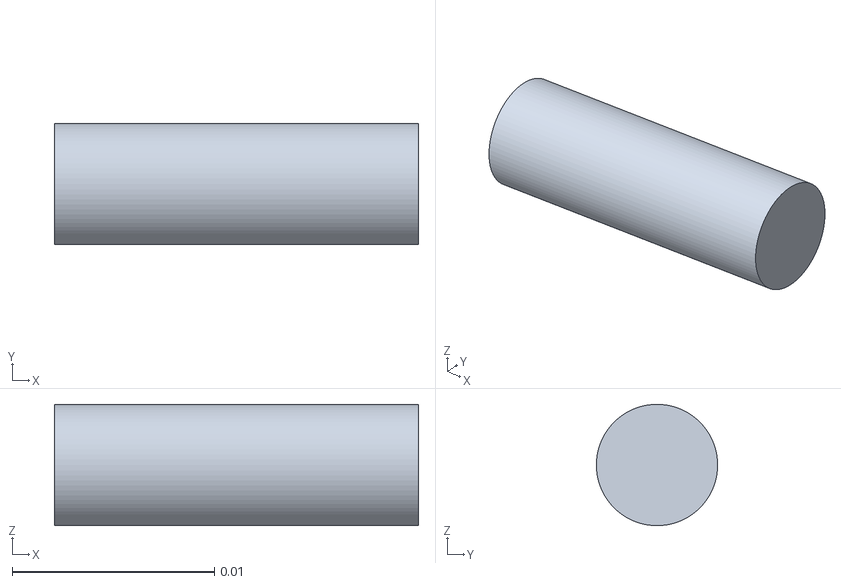
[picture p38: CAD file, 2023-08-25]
vscode/my-robot-longTail/shaft2.stl
0.018 x 0.006 x 0.006

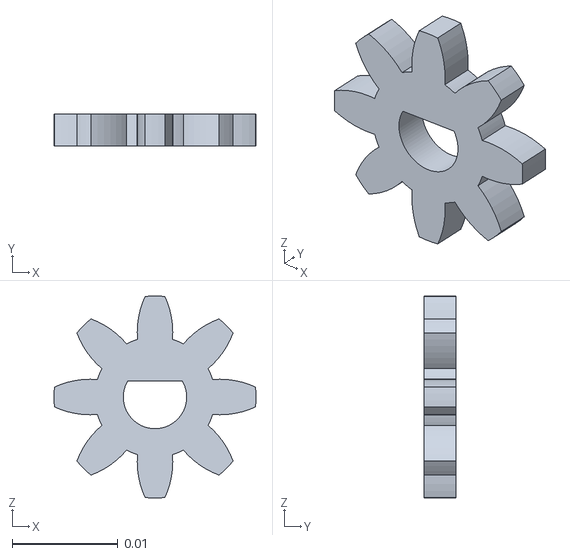
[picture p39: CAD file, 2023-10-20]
vscode/my-robot-newGears/spur_gear26.stl
0.0191 x 0.003 x 0.0191

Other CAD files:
inventor package/Templates/English/ANSI (in).dwg
inventor package/Templates/Metric/JIS.dwg
inventor package/Templates/Standard.dwg
inventor package/Templates/Metric/ANSI (mm).dwg
Drawing-files/v1/12x - standoff1.dxf
Drawing-files/v1/1x - back plate.dxf
Drawing-files/v1/1x - front plate.dxf
Drawing-files/v1/24x - standoff2.dxf
Drawing-files/v1/2x - Sun Gear.dxf
Drawing-files/v1/2x - bottom plate.dxf
Drawing-files/v1/2x - side plate.dxf
Drawing-files/v1/4x - Idler Gear.dxf
Drawing-files/v1/4x - Planet Gear.dxf
Drawing-files/v1/4x - frame.dxf
Drawing-files/v1/4x - tail fin.dxf
Drawing-files/v1/4x - wheel.dxf
Drawing-files/v2/12x - STANDOFF THICK - 3mm Acrylic.dxf
Drawing-files/v2/1x - BACK PLATE - 3mm MDF.dxf
Drawing-files/v2/1x - FRONT PLATE - 3mm MDF.dxf
Drawing-files/v2/24x - STANDOFF THIN - 3mm Acrylic.dxf
Drawing-files/v2/2x - BOTTOM PLATE - 3mm MDF.dxf
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

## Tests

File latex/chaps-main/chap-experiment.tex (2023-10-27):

\chapter{Experiment}

In order to validate that the model is accurate for each motion, the torque that causes the device to perform each motion is determined experimentally. The equivalent values produced by the model can be compared with the measured torques to validate the model quantitatively. However, the torque produced by a DC motor cannot be measured or set directly. The torque of a DC motor is proportional to the current running through it, and when the motor isn't moving, the current is proportional to the voltage across the motor terminals.

\section{Voltage-torque calibration} \label{sec:Voltage-torque calibration}
The relationship between terminal voltage and stalling torque is determined experimentally, this will allow subsequent experiments to measure the terminal voltage and calculate the stalling torque.
To characterise the motors, an experiment was set up to determine the stalling torque produced at different input voltages. In this experiment, the motor lifts a lever with a mass attached. The torque required to lift the lever increases as the lever angle increases, until the motor can no longer provide enough torque and stalls. The lever angle which causes the motor to stall can be used to calculate the stalling torque, specifically by using the horizontal displacement of the mass,
\begin{equation}
	T_\mathrm{Stall} = m g s_x
\end{equation}
where $T_\mathrm{Stall}$ is the stalling torque, $m$ is the mass attached to the lever, $g$ is the gravitational acceleration, and $s_x$ is the horizontal displacement between the mass and the motor axis. The experiment set-up is illustrated in Figure \ref{fig:lever-labelled}.
\begin{figure}[!h]
	\centering
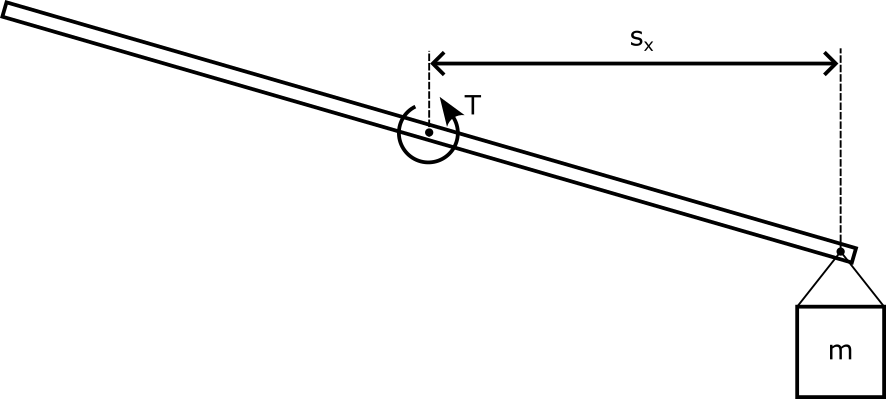
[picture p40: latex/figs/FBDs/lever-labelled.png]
	
	\caption{Calibration lever set-up.}
	\label{fig:lever-labelled}
\end{figure}
This test is repeated with different motor voltages.\\

\subsection{Variables}
Independent variable:\\
$\bullet$ Motor voltage (V)\\
Dependent variable:\\
$\bullet$ Distance the weight is lifted (mm)\\
Controlled variables:\\
$\bullet$ Motor used\\
$\bullet$ Lever used\\
$\bullet$ Power supply used\\
$\bullet$ Multimeter used\\
$\bullet$ Ruler used\\

\subsection{Method}

\begin{enumerate}
	\item Remove LIM from motor axle.
	\item Attach the lever to the motor axle.
	\item Measure the weight of the mass on a calibrated scale. \label{stepMeasure}
	\item Drive the motor until the lever is pointing straight down.
	\item Attach the mass to the lever.
	\item Adjust the voltage of the power supply to the chosen value. \label{stepAdjust}
	\item Power on the motor.
	\item Wait until the lever stops moving.
	\item Record the voltage across the motor terminals. 
	\item Quickly power off the motor. Leaving the motor on while stalling can cause damage to the motor.
	\item Measure the horizontal distance that the lever has moved.
	\item Drive the motor until the lever is pointing straight down. \label{stepReset}
	\item Repeat steps \ref{stepAdjust} to \ref{stepReset} with different power supply voltages.
	\item Remove the mass from the lever. \label{stepRemove}
	\item Repeat steps \ref{stepMeasure} to \ref{stepRemove} with different masses.
\end{enumerate}
\subsection{Results}
The measured results, as well as the calculated torque, are shown in Table \ref{voltage-torque-table}, and visualised in Figure \ref{torque-voltage-plot}.

\begin{table}[!ht]
	\centering
	\caption{Recorded results and calculated torque from the calibration experiment.}
	\label{voltage-torque-table}
	\begin{tabular}{|l|l|l|l|}
		\hline
		Mass (g) & Lever (mm) & Voltage (V) & Torque (N$\cdot$m) \\ \hline
		145 & 97 & 0.83 & 0.13797765 \\ \hline
		145 & 101 & 0.92 & 0.14366745 \\ \hline
		145 & 151 & 1.1 & 0.21478995 \\ \hline
		204 & 154 & 1.22 & 0.30819096 \\ \hline
		204 & 229 & 1.56 & 0.45828396 \\ \hline
		542 & 89 & 1.72 & 0.47321478 \\ \hline
		537 & 106 & 1.93 & 0.55840482 \\ \hline
		542 & 106 & 1.8 & 0.56360412 \\ \hline
		537 & 164 & 2.45 & 0.86394708 \\ \hline
		542 & 171 & 2.5 & 0.90921042 \\ \hline
		542 & 220 & 3 & 1.1697444 \\ \hline
		542 & 242 & 3.25 & 1.28671884 \\ \hline
		1289 & 117 & 3.5 & 1.47947553 \\ \hline
		1289 & 136 & 4 & 1.71973224 \\ \hline
		1289 & 160 & 4.5 & 2.0232144 \\ \hline
	\end{tabular}
\end{table}

\begin{figure}[!h]
	\centering
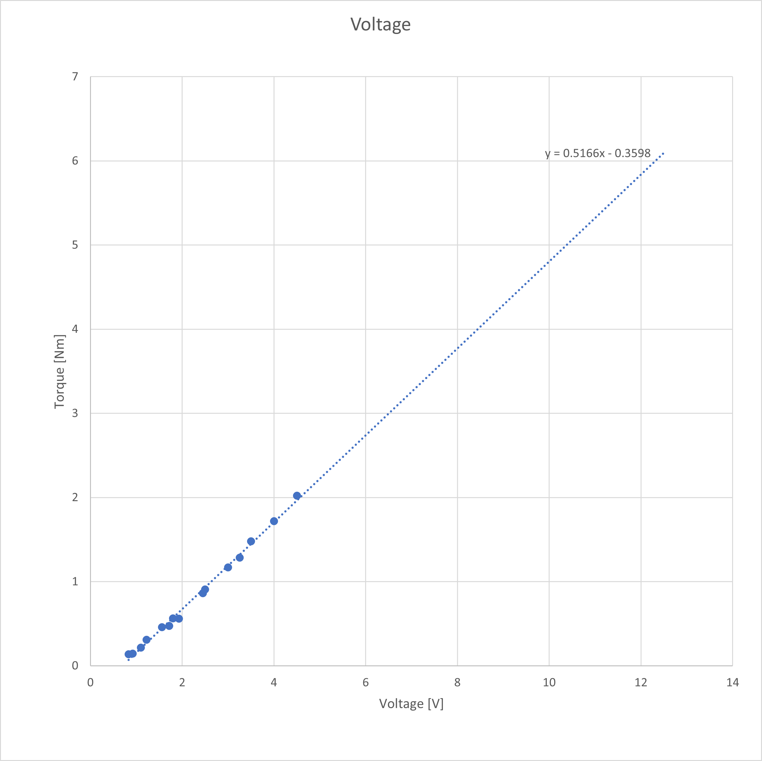
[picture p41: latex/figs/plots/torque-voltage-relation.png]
	
	\caption{Relationship between motor voltage and stalling torque.}
	\label{torque-voltage-plot}
\end{figure}

This plot shows a linear relationship between stalling torque and voltage, and gives the formula,
\begin{equation}
	T_\mathrm{Stall} =  0.5166 V - 0.3598 \label{eqTorqueVoltage}
\end{equation}
where $V$ is the motor terminal voltage.
This experiment did not attempt to measure torques beyond 2 N$\cdot$m as this risked damaging the device and was beyond the expected requirements for the device.

\section{Torque measurement}
This experiment aims to determine the torque required to lift the device through each stage of motion. The results of this experiment will be compared with the theoretical required torques provided by the model and the simulation. The device is placed in the starting position for each stage of motion and powered with a certain supply voltage. The motion of the device is then assessed. If the device does not move, the motion is marked as "None"; if the device starts to move but does not complete the stage of motion, it is marked as "Partial"; and if it completes the stage of motion, it is marked as "Full". For this experiment, bricks are stacked to create a staircase with a step height of 10 cm and width of 20 cm. The experimental set-up is shown in Figure \ref{fig:experiment-setup}.\\

\begin{figure}[!h]
	\centering
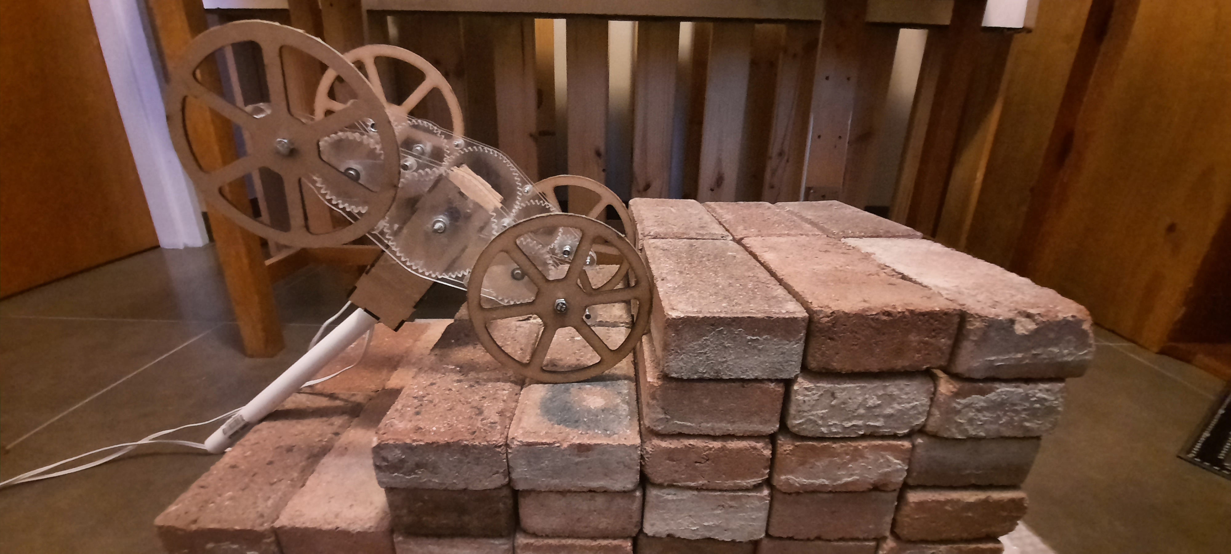
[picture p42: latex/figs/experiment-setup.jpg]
	
	\caption{Photograph of the experimental set-up, in which the device is performing Stage 4 motion.}
	\label{fig:experiment-setup}
\end{figure}

\subsection{Variables}
Independent variable:\\
$\bullet$ Motor voltage (V)\\
Dependent variable:\\
$\bullet$ Assessment of motion ("Full", "Partial", or "None")\\
Controlled variables:\\
$\bullet$ LIMed device\\
$\bullet$ Stairs\\
$\bullet$ Multimeter used\\

\subsection{Method}

\begin{enumerate}
	\item Place device in the starting position for the chosen stage of motion. \label{stepPlace}
	\item Adjust the voltage of the power supply to the chosen value.
	\item Power on the device.
	\item Observe how the device moves and classify the movement into "Full", "Partial", or "None". 
	\item Record the voltage across the motor terminals. 
	\item Power off the device.\label{stepOff}
	\item Repeat steps \ref{stepPlace} to \ref{stepOff} with a range of power supply voltages.\label{stepRepeatVoltage}
	\item Repeat steps \ref{stepPlace} to \ref{stepRepeatVoltage} for the different stages of motion.
\end{enumerate}

\subsection{Results}

Table \ref{tab:Stage1Torque} shows the measured results for the Stage 1 motion, as well as the torques calculated using Equation \ref{eqTorqueVoltage}. The data for the other stages of motion can be found in Appendix \ref{app:data}.

\begin{table}[!h]
	\centering
	\caption{Torque experiment results for Stage 1.}
	\label{tab:Stage1Torque}
	\begin{tabular}{|l|l|l|}
		\hline
		Voltage (V) & Assessment of motion & Torque (N$\cdot$m) \\ \hline
		0.89 & None & 0.099974 \\ \hline
		1.08 & None & 0.198128 \\ \hline
		1.12 & None & 0.218792 \\ \hline
		1.57 & None & 0.451262 \\ \hline
		1.68 & None & 0.508088 \\ \hline
		1.74 & None & 0.539084 \\ \hline
		1.81 & None & 0.575246 \\ \hline
		1.87 & None & 0.606242 \\ \hline
		1.89 & Partial & 0.616574 \\ \hline
		1.98 & Partial & 0.663068 \\ \hline
		2.05 & Partial & 0.69923 \\ \hline
		2.11 & Full & 0.730226 \\ \hline
		2.13 & Full & 0.740558 \\ \hline
		2.25 & Full & 0.80255 \\ \hline
		2.26 & Full & 0.807716 \\ \hline
		2.3 & Full & 0.82838 \\ \hline
	\end{tabular}
\end{table}

This data is plotted in Figure \ref{plotassessment-torque-relation-stage1}, which shows that the full motion only happens with torques of at least 0.73 N$\cdot$m, while partial motion only requires 0.61 N$\cdot$m.

\begin{figure}[h]
	\centering
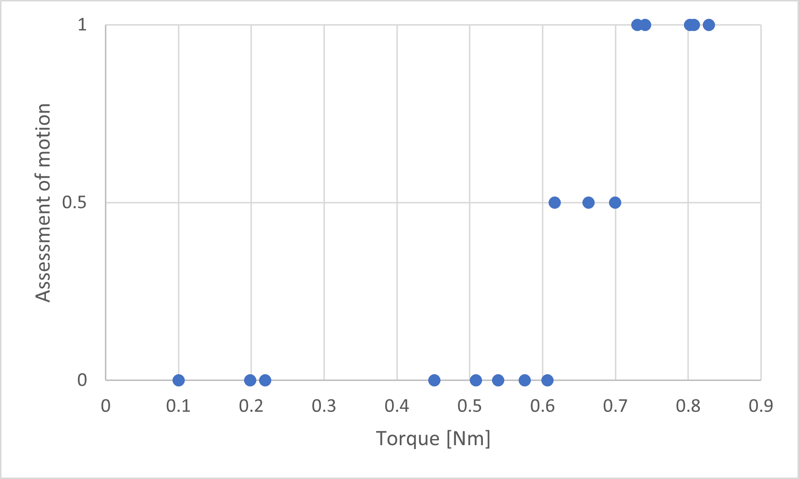
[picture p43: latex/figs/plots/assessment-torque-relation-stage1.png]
	
	\caption{Relationship between torque and motion for Stage 1, with 0, 0.5, and 1 representing "None", "Partial", and "Full" respectively.}
	\label{plotassessment-torque-relation-stage1}
\end{figure}

\clearpage
\section{Current measurement}
This experiment aims to measure the current running through the motors when the LIM climbs steps. Current is proportional to torque in DC motors, so the curve produced by this experiment can be compared with the simulated torque during the same movement. This will allow the kinematic aspects of the model and simulation to be validated, as the stalling torques from the previous experiment can only validate the statics. A 1 $\Omega$ resistor is placed in series with the motor, so that the voltage across the resistor will be equal to the current running through it.

\subsection{Variables}
Independent variable:\\
$\bullet$ Time (s)\\
Dependent variable:\\
$\bullet$ Current (A)\\
Controlled variables:\\
$\bullet$ LIM device used\\
$\bullet$ Power supply used\\
$\bullet$ Oscilloscope used\\
$\bullet$ Oscilloscope probes used\\
$\bullet$ Resistor used\\

\subsection{Method}

\begin{enumerate}
	\item Connect a 1 $\Omega$ resistor in series with one motor.
	\item Attach the oscilloscope probe to either end of the resistor.
	\item Configure the oscilloscope trigger on a rising edge with a 5 second period.
	\item Place the device against a step or wall so that it will perform Stage 1 motion when powered.
	\item Power on the device until it has completed Stage 1 motion.
	\item Record the voltage data from the oscilloscope.
\end{enumerate}

\subsection{Results}

Figure \ref{fig:current-stage-1} shows the plot recorded by the oscilloscope. It shows that there is a large spike in current as the device powers on, followed by a fairly constant but noisy current until a slight dip at 2.7 s, then a drop when it completes Stage 1 at 3.25 s. The spike at the start is due the motor producing no counter-electromotive force (EMF) when it is stationary. As the motor shaft initially accelerates, the current rapidly drops due to the counter-EMF produced by the motor. The noise shown in the plot can be attributed to the constant switching of the brushed DC motor. The noise could be eliminated by implementing a low pass filter, but this would also filter out the initial spike. 
\begin{figure}[h]
	\centering
	
	\caption{Current recorded over time as the device completes Stage 1.}
	\label{fig:current-stage-1}
\end{figure}

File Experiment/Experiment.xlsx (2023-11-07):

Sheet: movement1 40rpm
10x20 | 30 cm tail |  |  |  |  |  | 10x20
 | Voltage | Climbing? | torque | Key |  | notes: |  | 60cm tail
 | 1.79 | 0 | 0.246367 | 0 | no movement | 5.3 V -> 0.763 Nm |  | Voltage | Climbing? | torque
 | 2.4 | 0 | 0.33622 | 0.5 | Partial movement, one lim lifts |  |  | 5.67 | 0.5 | 0.817891
 | 3.11 | 0 | 0.440803 | 1 | full climbing |  |  | 5.8 | 0.5 | 0.83704
 | 4.5 | 0 | 0.64555 |  |  |  |  | 5.3 | 0 | 0.76339
 | 5.11 | 0 | 0.735403 |  |  |  |  | 4.97 | 0 | 0.714781
 | 6.6 | 1 | 0.95488 |  |  |  |  | 5.34 | 0 | 0.769282
 | 6 | 1 | 0.8665 |  |  |  |  | 5.18 | 0 | 0.745714
 | 5.39 | 0.5 | 0.776647 |  |  |  |  | 5.5 | 0 | 0.79285
 | 5.46 | 0.5 | 0.786958 |  |  |  |  | 6.09 | 1 | 0.879757
 | 5.42 | 1 | 0.781066 |  |  |  |  | 5.65 | 0.5 | 0.814945
 | 5.44 | 1 | 0.784012 |  |  |  |  | 5.9 | 0.5 | 0.85177
 | 4.76 | 0 | 0.683848 |  |  |  |  | 5.99 | 1 | 0.865027
 | 4.99 | 0 | 0.717727 |  |  |  |  | 6.04 | 1 | 0.872392
 | 5 | 0 | 0.7192 |  |  |  |  | 6.01 | 1 | 0.867973
 | 5.19 | 0.5 | 0.747187 |  |  |  |  | 5.64 | 0.5 | 0.813472
 | 5.13 | 0 | 0.738349 |  |  |  |  | 5.42 | 0 | 0.781066
 | 5.35 | 1 | 0.770755 |  |  |  |  | 5.48 | 0 | 0.789904
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

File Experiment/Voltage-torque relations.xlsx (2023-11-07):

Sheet: torque measurements 40rpm 100hz
Lever (mm) | Mass (g) | PWM (%) | Torque (Nm)
210 | 57 | 9 | 0.1174257
210 | 108 | 12 | 0.2224908
210 | 159 | 14 | 0.3275559
210 | 262 | 15 | 0.5397462
210 | 337 | 27 | 0.6942537
210 | 391 | 28 | 0.8054991
210 | 416 | 32 | 0.8570016
210 | 467 |  | 0.9620667
210 | 443 | 70 | 0.9126243
210 | 418 | 72 | 0.8611218
210 |  |  | 0
210 |  |  | 0
210 |  |  | 0
210 |  |  | 0
210 |  |  | 0
210 |  |  | 0
210 |  |  | 0
210 |  |  | 0
210 |  |  | 0
210 |  |  | 0
210 |  |  | 0
210 |  |  | 0
210 |  |  | 0
210 |  |  | 0
210 |  |  | 0

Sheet: torque measurements 6rpm
Lever (mm) | Mass (g) | Voltage | Torque (Nm)
210 | 748 | 4.6 | 1.5409548
210 |  |  | 0
210 | 441 | 3.5 | 0.9085041
210 | 310 | 2.4 | 0.638631
210 | 361 | 2.55 | 0.7436961
210 | 427 | 3.2 | 0.8796627
210 |  |  | 0
210 |  |  | 0
210 |  |  | 0
210 |  |  | 0
210 |  |  | 0
210 |  |  | 0
210 |  |  | 0
210 |  |  | 0
210 |  |  | 0
210 |  |  | 0
210 |  |  | 0
210 |  |  | 0
210 |  |  | 0
210 |  |  | 0
210 |  |  | 0
210 |  |  | 0
210 |  |  | 0
210 |  |  | 0
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

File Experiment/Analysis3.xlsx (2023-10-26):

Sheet: Sheet1
 |  | Stage
 |  | 1 | 1 | 3 | 3 | 4 | 4 | 6 | 6
 |  | partial | full | partial | full | partial | full | partial | full
default | Model | 0.52 | 0.52 | 0.31 | 0.52 | 0.67 | 0.77 | 0.35 | 0.69
 | Simulation | 0.53 | 0.68 | 0.41 | 0.48 | 0.54 | 0.84 | 0.47 | 0.59
 | Experiment | 0.62 | 0.73 | 0.39 | 0.39 | 0.78 | 0.89 | 0.62 | 0.78
60cm tail | model | 0.58 | 0.58 | 0.33 | 0.58 | 0.7 | 0.75 | 0.38 | 0.77
 | simulation | 0.71 | 0.8 | 0.56 | 0.56 | 0.8 | 0.85 | 0.48 | 0.6
 | experiment | 0.71 | 0.75 | 0.39 | 0.48 | 0.78 | 0.95 | 0.61 | 0.78
343g mass | model | 0.62 | 0.62 | 0.37 | 0.62 | 0.85 | 1.13 | 0.45 | 0.99
 | simulation | 0.67 | 0.87 | 0.52 | 0.6 | 0.71 | 1.07 | 0.63 | 0.7
 | experiment | 0.84 | 0.89 | 0.47 | 0.53 | 0.9 | 1.26 | 0.65 | 0.91
15cm step height | model
 | simulation
 | experiment
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

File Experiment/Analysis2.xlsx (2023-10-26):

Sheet: Sheet1
 |  | Stage
 |  | 1 | 1 | 3 | 3 | 4 | 4 | 6 | 6
 |  | partial | full | partial | full | partial | full | partial | full
default | Model | 0.52 | 0.52 | 0.31 | 0.52 | 0.67 | 0.77 | 0.35 | 0.69
 | Simulation | 0.53 | 0.68 | 0.41 | 0.48 | 0.54 | 0.84 | 0.47 | 0.59
 | Experiment | 0.62 | 0.73 | 0.39 | 0.39 | 0.78 | 0.89 | 0.62 | 0.78
60cm tail | model | 0.58 | 0.58 | 0.33 | 0.58 | 0.7 | 0.75 | 0.38 | 0.77
 | simulation | 0.71 | 0.8 | 0.56 | 0.56 | 0.8 | 0.85 | 0.48 | 0.6
 | experiment | 0.71 | 0.75 | 0.39 | 0.48 | 0.78 | 0.95 | 0.61 | 0.78
343g mass | model | 0.62 | 0.62 | 0.37 | 0.62 | 0.85 | 1.13 | 0.45 | 0.99
 | simulation | 0.67 | 0.87 | 0.52 | 0.6 | 0.71 | 1.07 | 0.63 | 0.7
 | experiment | 0.84 | 0.89 | 0.47 | 0.53 | 0.9 | 1.26 | 0.65 | 0.91
15cm step height | model
 | simulation
 | experiment
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

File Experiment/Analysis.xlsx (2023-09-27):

 |  | stage1 |  | stage3 |  | stage4 |  | stage6
 |  | partial | full | partial | full | partial | full | partial | full
default | model
 | simulation | 0.53 | 0.68
 | experiment | 0.62 | 0.73 | 0.39 | 0.39 | 0.78 | 0.89
60cm tail | model
 | simulation | 0.71 | 0.8 | 0.56 | 0.56 | 0.8 | 0.85
 | experiment | 0.71 | 0.75 | 0.39 | 0.48 | 0.78 | 0.95
343g mass | model
 | simulation | 0.67 | 0.87 | 0.52 | 0.6 | 0.71 | 1.07
 | experiment | 0.84 | 0.89 | 0.47 | 0.53 | 0.9 | 1.26 |  | 0.91
15cm step height | model
 | simulation
 | experiment

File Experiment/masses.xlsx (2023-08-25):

item | masses (g)
jgy 6 rpm | 156 | 412
jgy 40 rpm | 150
housing mdf | 106
LIM1 | 300
Lim2 | 299
housing assembled dangling cable | 484
4X IDLER GEAR | 74
4X IDLER GEAR + SHAFTS | 81
2X SHAFT+EXTENSION | 30
TAIL 30CM | 40
TAIL 60CM | 83

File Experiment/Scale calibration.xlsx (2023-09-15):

kitchen scale | SAM scale
336 | 336
538 | 538
202 | 202
145 | 145
52 | 52
94 | 94
23 | 24
77 | 77
57 | 57
43 | 43

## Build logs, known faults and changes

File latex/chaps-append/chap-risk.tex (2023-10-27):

\chapter{Risk Assessment}

The device uses a maximum voltage of 12 V, which is considered safe to touch. Gears are enclosed within the frame of the LIMs, however power should still be disconnected when handling the device as the geared motors can produce significant torque. To prevent motor burnout, they should not be left stalling for more than a few seconds at a time.\\

\noindent The main risk to the feasibility of the project was that there would not be enough time to build a fully functioning robot platform. The projects preceding this one all encountered complications when building robot platforms that they were unable to solve within the time constraints of their projects. This risk was mitigated by completing activities in a timely manner as described in the Gantt Chart, as well as careful planning and consideration of previous pitfalls.
\\

\noindent There was also the risk that it would be impossible to create a closed form model to describe the dynamics of the system. Fortunately, this was not the case.\\

\noindent There was a risk that the project would exceed the allowed cost. This is because the prototype may have required hardware such as high powered motors, custom parts, encoders, controllers, and possibly batteries, which could have a considerable cost. This was be mitigated simplifying the design to only use the minimum hardware required to build a prototype.\\

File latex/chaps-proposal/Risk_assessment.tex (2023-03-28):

\chapter{Risk Assessment}

The main risk to the feasibility of the project is that there will not be enough time to build a fully functioning robot platform. The projects preceding this one all encountered complications when building robot platforms that they were unable to solve within the time constraints of their projects. This risk will be mitigated by completing activities in a timely manner as described in the Gantt. Chart, as well as careful planning and consideration of previous pitfalls.
\\

\noindent There is also the risk that it will be impossible to create a closed form model to describe the dynamics of the system. If this is the case, simplifications and numerical methods will be used to produce the model.\\

\noindent There is a considerable risk that the project will exceed the allowed cost. This is because the prototype may require hardware such as high powered motors, custom parts, encoders, controllers, and possibly batteries, which may have a considerable cost. This will be mitigated by using hardware from the university where possible, as well as carefully considering the cost of components.\\

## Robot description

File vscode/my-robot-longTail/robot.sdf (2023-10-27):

<sdf version="1.6">
<model name="onshape">
<link name="body">
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
<inertial>
<pose>-4.2700195396606548134e-06 0.24038255533869221092 0.070865629432002558152 0 0 0</pose>
<mass>0.43095538069190569841</mass>
<inertia><ixx>0.0058549609510841647483</ixx><ixy>-1.475275488986761994e-07</ixy><ixz>-3.7035047746885835191e-06</ixz><iyy>0.00027867573259774791172</iyy><iyz>0.00043666991150742356584</iyz><izz>0.0059440084638499928946</izz></inertia>
</inertial>
</link>

<link name="main_shaft">
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
<inertial>
<pose>0.056467310588740417254 0.18634796984563217759 0.074996299416563841356 0 0 0</pose>
<mass>0.056167152496905625725</mass>
<inertia><ixx>3.4375920868575290923e-05</ixx><ixy>2.4123592434306141898e-09</ixy><ixz>1.7168502372076122237e-10</ixz><iyy>2.1613959966131506853e-05</iyy><iyz>4.6651301254371629241e-10</iyz><izz>2.1607433572334923839e-05</izz></inertia>
</inertial>
</link>

<link name="lim_frame">
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
<inertial>
<pose>0.061671566059199857401 0.18640000000000273017 0.075000000000000441314 0 0 0</pose>
<mass>0.13271340229034475633</mass>
<inertia><ixx>0.00076846598232952964547</ixx><ixy>-5.8546606604499649205e-17</ixy><ixz>1.4524529516291851494e-18</ixz><iyy>5.6474718491939252115e-05</iyy><iyz>-6.0298157932665505387e-18</iyz><izz>0.00072176790821096065056</izz></inertia>
</inertial>
</link>

<link name="idler">
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
<inertial>
<pose>0.06059999999999183401 0.11620206579860477281 0.075029186483818344211 0 0 0</pose>
<mass>0.018874380082186052732</mass>
<inertia><ixx>6.6879087944629088885e-06</ixx><ixy>3.7021625443374575757e-13</ixy><ixz>5.2305767914762877763e-12</ixz><iyy>3.4386675697004278387e-06</iyy><iyz>-8.7363950397048585824e-12</iyz><izz>3.438544756540699166e-06</izz></inertia>
</inertial>
</link>

<joint name="idler_a" type="revolute">
<pose>0.057099999999991858657 0.1162000000000029537 0.074999999999999886202 -1.5707963267948594765 0.07066144949931001118 1.5707963267948152897</pose>
<parent>lim_frame</parent>
<child>idler</child>
<axis>
<xyz>0 0 1</xyz>
<limit><effort>1</effort><velocity>20</velocity></limit>
</axis>
</joint>

<link name="idler_2">
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
<inertial>
<pose>0.060600000000003463596 0.2565929448053993478 0.075028396172114236728 0 0 0</pose>
<mass>0.018874380082186052732</mass>
<inertia><ixx>6.687908794462920747e-06</ixx><ixy>-1.2643779325353457027e-12</ixy><ixz>5.0889432028744762086e-12</ixz><iyy>3.4386609756446960444e-06</iyy><iyz>2.9028948434451419109e-11</iyz><izz>3.4385513505964330779e-06</izz></inertia>
</inertial>
</link>

<joint name="idler_b" type="revolute">
<pose>0.057100000000003536815 0.25660000000000293685 0.075000000000001301736 -1.5707963267948583663 -0.24352480249659719247 1.570796326794801745</pose>
<parent>lim_frame</parent>
<child>idler_2</child>
<axis>
<xyz>0 0 1</xyz>
<limit><effort>1</effort><velocity>20</velocity></limit>
</axis>
</joint>

<link name="wheel_shaft">
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
<inertial>
<pose>0.068328033501865462207 0.29779551908844270613 0.075000000000001121325 0 0 0</pose>
<mass>0.05463272607293223615</mass>
<inertia><ixx>6.11692586014166037e-05</ixx><ixy>-7.0623900425473054081e-09</ixy><ixz>3.4597573056687822576e-19</ixz><iyy>3.5799871878553662149e-05</iyy><iyz>-3.4803683360114416259e-20</iyz><izz>3.5799503574986235696e-05</izz></inertia>
</inertial>
</link>

<joint name="wheel_a" type="revolute">
<pose>0.057100000000006964629 0.29780000000000289573 0.075000000000001704192 -1.5707963267948592545 0.29856254452159236568 1.570796326794826836</pose>
<parent>lim_frame</parent>
<child>wheel_shaft</child>
<axis>
<xyz>0 0 1</xyz>
<limit><effort>1</effort><velocity>20</velocity></limit>
</axis>
</joint>

<link name="wheel_shaft_2">
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
<inertial>
<pose>0.06832803350186487934 0.074995519088442694211 0.074999999999998803735 0 0 0</pose>
<mass>0.05463272607293223615</mass>
<inertia><ixx>6.116925860141665791e-05</ixx><ixy>-7.0623900425885345713e-09</ixy><ixz>4.2194057563904742223e-19</ixz><iyy>3.5799871878553553729e-05</iyy><iyz>-8.2706458785150253857e-21</iyz><izz>3.5799503574986195039e-05</izz></inertia>
</inertial>
</link>

<joint name="wheel_b" type="revolute">
<pose>0.057100000000006478906 0.075000000000002620126 0.074999999999999469869 -1.5707963267948577002 0.29856254452159264323 1.5707963267948257258</pose>
<parent>lim_frame</parent>
<child>wheel_shaft_2</child>
<axis>
<xyz>0 0 1</xyz>
<limit><effort>1</effort><velocity>20</velocity></limit>
</axis>
</joint>

<joint name="sun_b" type="revolute">
<pose>0.057099999999997701206 0.18640000000000292446 0.075000000000000580092 -1.5707963267949336394 9.886056034444388184e-15 -1.5707963267949798247</pose>
<parent>main_shaft</parent>
<child>lim_frame</child>
<axis>
<xyz>0 0 1</xyz>
<limit><effort>1</effort><velocity>20</velocity></limit>
</axis>
</joint>

<joint name="motor_b" type="revolute">
<pose>0.02874999999999805142 0.1864000000000050894 0.075000000000001565414 1.570796326795419029 1.4997907099114997642 1.570796326795334652</pose>
<parent>body</parent>
<child>main_shaft</child>
<axis>
<xyz>0 0 1</xyz>
<limit><effort>1</effort><velocity>20</velocity></limit>
</axis>
</joint>

<link name="main_shaft_2">
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
<inertial>
<pose>-0.056467310588745205091 0.1864222992974769455 0.074952845227031536512 0 0 0</pose>
<mass>0.056167152496905625725</mass>
<inertia><ixx>3.437592086857546033e-05</ixx><ixy>1.0338040210770507894e-09</ixy><ixz>-2.1863673337413193671e-09</ixz><iyy>2.1608605306363335276e-05</iyy><iyz>-2.547915118423119751e-09</iyz><izz>2.1612788232103925508e-05</izz></inertia>
</inertial>
</link>

<link name="lim_frame_2">
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
<inertial>
<pose>-0.061671566059204721566 0.18640000000000175873 0.075000000000001815215 0 0 0</pose>
<mass>0.13271340229034478408</mass>
<inertia><ixx>0.00076846598232952801916</ixx><ixy>-2.4709539258184042704e-18</ixy><ixz>-1.4258762283561622967e-18</ixz><iyy>5.6474718491940478619e-05</iyy><iyz>-1.1503792456237600959e-17</iyz><izz>0.00072176790821097496203</izz></inertia>
</inertial>
</link>

<link name="idler_3">
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
<inertial>
<pose>-0.060600000000002970935 0.11621787692399658531 0.075029044997768648551 0 0 0</pose>
<mass>0.018874380082186049262</mass>
<inertia><ixx>6.6879087944629165118e-06</ixx><ixy>2.7485333212337167206e-12</ixy><ixz>4.465597338161783621e-12</ixz><iyy>3.4386341057565596003e-06</iyy><iyz>-5.5374197444288682799e-11</iyz><izz>3.4385782204845767217e-06</izz></inertia>
</inertial>
</link>

<joint name="idler_c" type="revolute">
<pose>-0.057100000000002947009 0.11620000000000212104 0.075000000000000677236 1.5707963267948970021 0.55173187410380153395 1.570796326794896558</pose>
<parent>lim_frame_2</parent>
<child>idler_3</child>
<axis>
<xyz>0 0 1</xyz>
<limit><effort>1</effort><velocity>20</velocity></limit>
</axis>
</joint>

<link name="idler_4">
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
<inertial>
<pose>-0.060600000000002832157 0.256617876924001731 0.075029044997771007774 0 0 0</pose>
<mass>0.018874380082186052732</mass>
<inertia><ixx>6.6879087944629173588e-06</ixx><ixy>2.7485333250654338066e-12</ixy><ixz>4.4655973377606333356e-12</ixz><iyy>3.4386341057565621414e-06</iyy><iyz>-5.5374197444289639226e-11</iyz><izz>3.4385782204845792628e-06</izz></inertia>
</inertial>
</link>

<joint name="idler_d" type="revolute">
<pose>-0.057100000000002884559 0.25660000000000748877 0.075000000000002897682 1.5707963267948970021 0.55173187410380153395 1.570796326794896558</pose>
<parent>lim_frame_2</parent>
<child>idler_4</child>
<axis>
<xyz>0 0 1</xyz>
<limit><effort>1</effort><velocity>20</velocity></limit>
</axis>
</joint>

<link name="wheel_shaft_3">
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
<inertial>
<pose>-0.068328033501860896415 0.29780059898222543957 0.074995559303132355855 0 0 0</pose>
<mass>0.05463272607293223615</mass>
<inertia><ixx>6.1169258601416752778e-05</ixx><ixy>-9.4405925919338325973e-10</ixy><ixz>6.999007446334084647e-09</ixz><iyy>3.5799510156127500513e-05</iyy><iyz>-4.8790833445871691802e-11</iyz><izz>3.5799865297417601503e-05</izz></inertia>
</inertial>
</link>
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

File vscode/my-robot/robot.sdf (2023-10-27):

<sdf version="1.6">
<model name="onshape">
<link name="body">
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
<inertial>
<pose>-4.2700195408687042142e-06 0.22962121125965584412 0.068557509902109625699 0 0 0</pose>
<mass>0.43095538069190569841</mass>
<inertia><ixx>0.002456738120531125856</ixx><ixy>-3.9288268715759562931e-07</ixy><ixz>-3.6863189835539571195e-06</ixz><iyy>0.0002959617421038759303</iyy><iyz>0.00034039263996705413891</iyz><izz>0.0025284996237907933492</izz></inertia>
</inertial>
</link>

<link name="main_shaft">
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
<inertial>
<pose>0.056467310588742672395 0.18634796984563217759 0.0749962994165638136 0 0 0</pose>
<mass>0.056167152496905625725</mass>
<inertia><ixx>3.4375920868575290923e-05</ixx><ixy>2.4123592434306158442e-09</ixy><ixz>1.7168502372076145502e-10</ixz><iyy>2.1613959966131503465e-05</iyy><iyz>4.6651301254347599645e-10</iyz><izz>2.1607433572334927227e-05</izz></inertia>
</inertial>
</link>

<link name="lim_frame">
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
<inertial>
<pose>0.061671566059202445609 0.18640000000000270242 0.075000000000000427436 0 0 0</pose>
<mass>0.13271340229034475633</mass>
<inertia><ixx>0.00076846598232952975389</ixx><ixy>-5.8533998821000692527e-17</ixy><ixz>1.4627926575873097108e-18</ixz><iyy>5.6474718491939231786e-05</iyy><iyz>-6.0298157932665505387e-18</iyz><izz>0.00072176790821096075898</izz></inertia>
</inertial>
</link>

<link name="idler">
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
<inertial>
<pose>0.060599999999994401401 0.11620206579860481444 0.075029186483818316455 0 0 0</pose>
<mass>0.018874380082186052732</mass>
<inertia><ixx>6.6879087944629088885e-06</ixx><ixy>3.702162544337589347e-13</ixy><ixz>5.2305767914764889169e-12</ixz><iyy>3.4386675697004282622e-06</iyy><iyz>-8.7363950397048569668e-12</iyz><izz>3.438544756540699166e-06</izz></inertia>
</inertial>
</link>

<joint name="idler_a" type="revolute">
<pose>0.057099999999994432986 0.11620000000000298146 0.074999999999999858447 -1.5707963267948594765 0.07066144949931001118 1.5707963267948152897</pose>
<parent>lim_frame</parent>
<child>idler</child>
<axis>
<xyz>0 0 1</xyz>
<limit><effort>1</effort><velocity>20</velocity></limit>
</axis>
</joint>

<link name="idler_2">
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
<inertial>
<pose>0.060600000000006024048 0.2565929448053993478 0.075028396172114208973 0 0 0</pose>
<mass>0.018874380082186052732</mass>
<inertia><ixx>6.687908794462920747e-06</ixx><ixy>-1.2643779325353971995e-12</ixy><ixz>5.0889432028746741181e-12</ixz><iyy>3.4386609756446960444e-06</iyy><iyz>2.9028948434451415878e-11</iyz><izz>3.4385513505964330779e-06</izz></inertia>
</inertial>
</link>

<joint name="idler_b" type="revolute">
<pose>0.057100000000006111145 0.25660000000000299236 0.075000000000001273981 -1.5707963267948583663 -0.24352480249659719247 1.570796326794801745</pose>
<parent>lim_frame</parent>
<child>idler_2</child>
<axis>
<xyz>0 0 1</xyz>
<limit><effort>1</effort><velocity>20</velocity></limit>
</axis>
</joint>

<link name="wheel_shaft">
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
<inertial>
<pose>0.068328033501868043476 0.29779551908844270613 0.075000000000001107447 0 0 0</pose>
<mass>0.05463272607293223615</mass>
<inertia><ixx>6.11692586014166037e-05</ixx><ixy>-7.0623900425473045809e-09</ixy><ixz>3.4597573056687870724e-19</ixz><iyy>3.5799871878553662149e-05</iyy><iyz>-3.4803683360114434315e-20</iyz><izz>3.5799503574986235696e-05</izz></inertia>
</inertial>
</link>

<joint name="wheel_a" type="revolute">
<pose>0.057100000000009545897 0.29780000000000295124 0.075000000000001690315 -1.5707963267948592545 0.29856254452159236568 1.570796326794826836</pose>
<parent>lim_frame</parent>
<child>wheel_shaft</child>
<axis>
<xyz>0 0 1</xyz>
<limit><effort>1</effort><velocity>20</velocity></limit>
</axis>
</joint>

<link name="wheel_shaft_2">
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
<inertial>
<pose>0.068328033501867446731 0.074995519088442721967 0.074999999999998789857 0 0 0</pose>
<mass>0.05463272607293223615</mass>
<inertia><ixx>6.116925860141665791e-05</ixx><ixy>-7.0623900425885345713e-09</ixy><ixz>4.2194057563904790371e-19</ixz><iyy>3.5799871878553560505e-05</iyy><iyz>-8.2706458785150268903e-21</iyz><izz>3.5799503574986195039e-05</izz></inertia>
</inertial>
</link>
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

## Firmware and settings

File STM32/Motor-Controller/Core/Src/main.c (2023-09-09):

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
/* Includes ------------------------------------------------------------------*/
#include "main.h"

/* USER CODE BEGIN Includes */
#include <stdio.h>
#include <stdlib.h>
#include <string.h>
#include "INA219.h"
/* USER CODE END Includes */

/* USER CODE BEGIN PD */
#define THRESHOLD_OFF 0.2
#define THRESHOLD_FULL 0.90
#define SLIDERS 0
#define UART 1
#define INA_ADR1 0x40
/* USER CODE END PD */

ADC_HandleTypeDef hadc1;
DMA_HandleTypeDef hdma_adc1;

I2C_HandleTypeDef hi2c1;

TIM_HandleTypeDef htim1;
TIM_HandleTypeDef htim2;
TIM_HandleTypeDef htim3;

UART_HandleTypeDef huart2;

/* USER CODE BEGIN PV */
uint8_t UART_RX_Pos = 0;
uint8_t UART_RX_Message[100];
uint8_t UART_RX_Byte[1];
uint8_t UART_RX_Flag = 0;
int UART_RX_Motor_a;
int UART_RX_Motor_b;
volatile uint8_t TIM3_flag = 0;
uint32_t UART_Counter=0;

INA219_t ina219;

int16_t vbus, vshunt, current;
double currentmA;
/* USER CODE END PV */

void SystemClock_Config(void);
static void MX_GPIO_Init(void);
static void MX_DMA_Init(void);
static void MX_ADC1_Init(void);
static void MX_TIM1_Init(void);
static void MX_TIM2_Init(void);
static void MX_USART2_UART_Init(void);
static void MX_TIM3_Init(void);
static void MX_I2C1_Init(void);
/* USER CODE BEGIN PFP */
double clamp(double d, double min, double max);
void num2str(int num, uint8_t *string, int numdigits);
int str2num(uint8_t *string, int numdigits);
void HAL_UART_RxCpltCallback(UART_HandleTypeDef *huart);
void UART_RX_Handler(void);
/* USER CODE END PFP */

/**
  * @brief  The application entry point.
  * @retval int
  */
int main(void)
{
  /* MCU Configuration--------------------------------------------------------*/

  /* Reset of all peripherals, Initializes the Flash interface and the Systick. */
  HAL_Init();

  /* Configure the system clock */
  SystemClock_Config();

  /* Initialize all configured peripherals */
  MX_GPIO_Init();
  MX_DMA_Init();
  MX_ADC1_Init();
  MX_TIM1_Init();
  MX_TIM2_Init();
  MX_USART2_UART_Init();
  MX_TIM3_Init();
  MX_I2C1_Init();
  /* USER CODE BEGIN 2 */
	uint32_t ADC_Value[2];
	uint8_t txbuffer[200];

	uint8_t input = SLIDERS;
	HAL_UART_Receive_IT(&huart2, UART_RX_Byte, 1);
	HAL_TIM_Base_Start_IT(&htim1);
	HAL_TIM_Base_Start_IT(&htim3);
	HAL_ADC_Start_DMA(&hadc1, ADC_Value, 2); // start adc in DMA mode
	HAL_TIM_PWM_Start(&htim2, TIM_CHANNEL_1);
	HAL_TIM_PWM_Start(&htim2, TIM_CHANNEL_2);

	for (int i = 0; i < 100; i++) {
		txbuffer[i] = (uint8_t) *" ";
	}

	while (!INA219_Init(&ina219, &hi2c1, INA219_ADDRESS)) {

	}

	//INA219_setPowerMode(&ina219, INA219_CONFIG_MODE_ADCOFF);

	vbus = INA219_ReadBusVoltage(&ina219);
	vshunt = INA219_ReadShuntVolage(&ina219);
	current = INA219_ReadCurrent(&ina219);
  /* USER CODE END 2 */

  /* Infinite loop */
  /* USER CODE BEGIN WHILE */
	while (1) {
		double slider1 = (ADC_Value[0] / 2047.0) - 1.0;
		double slider2 = (ADC_Value[1] / 2047.0) - 1.0;

		if (input == SLIDERS) {
			if (slider1 > THRESHOLD_OFF) {
				HAL_GPIO_WritePin(Motor_a_fwd_GPIO_Port, Motor_a_fwd_Pin, 1);
				HAL_GPIO_WritePin(Motor_a_rev_GPIO_Port, Motor_a_rev_Pin, 0);
				TIM2->CCR1 = ((slider1 - THRESHOLD_OFF)
						/ (THRESHOLD_FULL - THRESHOLD_OFF)) * 999.0;
			} else if (slider1 < -THRESHOLD_OFF) {
				HAL_GPIO_WritePin(Motor_a_fwd_GPIO_Port, Motor_a_fwd_Pin, 0);
				HAL_GPIO_WritePin(Motor_a_rev_GPIO_Port, Motor_a_rev_Pin, 1);
				TIM2->CCR1 = ((-slider1 - THRESHOLD_OFF)
						/ (THRESHOLD_FULL - THRESHOLD_OFF)) * 999.0;
			} else {
				HAL_GPIO_WritePin(Motor_a_fwd_GPIO_Port, Motor_a_fwd_Pin, 0);
				HAL_GPIO_WritePin(Motor_a_rev_GPIO_Port, Motor_a_rev_Pin, 0);
				TIM2->CCR1 = 0;
			}

			if (slider2 > THRESHOLD_OFF) {
				HAL_GPIO_WritePin(Motor_b_fwd_GPIO_Port, Motor_b_fwd_Pin, 1);
				HAL_GPIO_WritePin(Motor_b_rev_GPIO_Port, Motor_b_rev_Pin, 0);
				TIM2->CCR2 = ((slider2 - THRESHOLD_OFF)
						/ (THRESHOLD_FULL - THRESHOLD_OFF)) * 999.0;
			} else if (slider2 < -THRESHOLD_OFF) {
				HAL_GPIO_WritePin(Motor_b_fwd_GPIO_Port, Motor_b_fwd_Pin, 0);
				HAL_GPIO_WritePin(Motor_b_rev_GPIO_Port, Motor_b_rev_Pin, 1);
				TIM2->CCR2 = ((-slider2 - THRESHOLD_OFF)
						/ (THRESHOLD_FULL - THRESHOLD_OFF)) * 999.0;
			} else {
				HAL_GPIO_WritePin(Motor_b_fwd_GPIO_Port, Motor_b_fwd_Pin, 0);
				HAL_GPIO_WritePin(Motor_b_rev_GPIO_Port, Motor_b_rev_Pin, 0);
				TIM2->CCR2 = 0;
			}
		} else if (input == UART) {

			if (UART_RX_Motor_a > 0) {
				HAL_GPIO_WritePin(Motor_a_fwd_GPIO_Port, Motor_a_fwd_Pin, 1);
				HAL_GPIO_WritePin(Motor_a_rev_GPIO_Port, Motor_a_rev_Pin, 0);
				TIM2->CCR1 = UART_RX_Motor_a;
			} else if (UART_RX_Motor_a < 0) {
				HAL_GPIO_WritePin(Motor_a_fwd_GPIO_Port, Motor_a_fwd_Pin, 0);
				HAL_GPIO_WritePin(Motor_a_rev_GPIO_Port, Motor_a_rev_Pin, 1);
				TIM2->CCR1 = -UART_RX_Motor_a;
			} else {
				HAL_GPIO_WritePin(Motor_a_fwd_GPIO_Port, Motor_a_fwd_Pin, 0);
				HAL_GPIO_WritePin(Motor_a_rev_GPIO_Port, Motor_a_rev_Pin, 0);
				TIM2->CCR1 = 0;
			}

			if (UART_RX_Motor_b > 0) {
				HAL_GPIO_WritePin(Motor_b_fwd_GPIO_Port, Motor_b_fwd_Pin, 1);
				HAL_GPIO_WritePin(Motor_b_rev_GPIO_Port, Motor_b_rev_Pin, 0);
				TIM2->CCR2 = UART_RX_Motor_b;
			} else if (UART_RX_Motor_b < 0) {
				HAL_GPIO_WritePin(Motor_b_fwd_GPIO_Port, Motor_b_fwd_Pin, 0);
				HAL_GPIO_WritePin(Motor_b_rev_GPIO_Port, Motor_b_rev_Pin, 1);
				TIM2->CCR2 = -UART_RX_Motor_b;
			} else {
				HAL_GPIO_WritePin(Motor_b_fwd_GPIO_Port, Motor_b_fwd_Pin, 0);
				HAL_GPIO_WritePin(Motor_b_rev_GPIO_Port, Motor_b_rev_Pin, 0);
				TIM2->CCR2 = 0;
			}
		}

		if (TIM3_flag == 1) {
			TIM3_flag = 0;
			vbus = INA219_ReadBusVoltage(&ina219);
			vshunt = INA219_ReadShuntVolage(&ina219);
			current = INA219_ReadCurrent(&ina219);
			UART_Counter +=1;
			sprintf((char*) txbuffer, "Duty Cycles: %04d, %04d\n"
					                  "Current:     %05.1f mA, %05.1f mA\n"
									  "Vbus:        %04d, %04d\n"
									  "Vshunt:      %04d, %04d\n", (int) TIM2->CCR1, (int) TIM2->CCR2, currentmA, currentmA, vbus, vbus, vshunt, vshunt);
//			sprintf((char*) txbuffer, "%d,%d\n", (int) UART_Counter, current);
			HAL_UART_Transmit(&huart2, txbuffer, strlen((char*) txbuffer), 50);
		}
		if (UART_RX_Flag == 1) {
			UART_RX_Handler();
		}
    /* USER CODE END WHILE */

    /* USER CODE BEGIN 3 */
	}
  /* USER CODE END 3 */
}

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
/* USER CODE BEGIN 4 */
double clamp(double d, double min, double max) {
	const double t = d < min ? min : d;
	return t > max ? max : t;
}

void num2str(int num, uint8_t *string, int numdigits) {
	int unit = 1;
	for (int i = 0; i < numdigits; i++) {
		string[numdigits - i - 1] = (num / unit) % 10 + 48;
		unit = unit * 10;
	}
}
int str2num(uint8_t *string, int numdigits) {
	int unit = 1;
	int num = 0;
	for (int i = 0; i < numdigits; i++) {
		num = num + (string[numdigits - i - 1] - 48) * unit;
		unit = unit * 10;
	}
	return num;
}
void HAL_UART_RxCpltCallback(UART_HandleTypeDef *huart) {
	UART_RX_Flag = 1;
	HAL_UART_Receive_IT(&huart2, UART_RX_Byte, 1);
}
void UART_RX_Handler(void) {
	UART_RX_Flag = 0;
	UART_RX_Message[UART_RX_Pos] = UART_RX_Byte[0];
	UART_RX_Pos += 1;
	if (UART_RX_Byte[0] == (uint8_t) *"\n") {
		if (UART_RX_Message[0] == (uint8_t) *"+") {
			UART_RX_Motor_a = str2num(&UART_RX_Message[1], 3);
		} else if (UART_RX_Message[0] == (uint8_t) *"-") {
			UART_RX_Motor_a = -str2num(&UART_RX_Message[1], 3);
		}
		if (UART_RX_Message[5] == (uint8_t) *"+") {
			UART_RX_Motor_b = str2num(&UART_RX_Message[6], 3);
		} else if (UART_RX_Message[5] == (uint8_t) *"-") {
			UART_RX_Motor_b = -str2num(&UART_RX_Message[6], 3);
		}
		if (UART_RX_Message[10] == (uint8_t) *"P") {
			TIM2->PSC = str2num(&UART_RX_Message[11], 3) - 1;
		}
		UART_RX_Pos = 0;
	}
}
/* USER CODE END 4 */
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


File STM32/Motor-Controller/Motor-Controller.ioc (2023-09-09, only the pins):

Mcu.UserName=STM32F303RETx
PA0.Signal=ADC1_IN1
PA1.Signal=ADC1_IN2
PA13.Signal=SYS_JTMS-SWDIO
PA14.Signal=SYS_JTCK-SWCLK
PA15.Signal=S_TIM2_CH1_ETR
PA2.Signal=USART2_TX
PA3.Signal=USART2_RX
PB3.Signal=S_TIM2_CH2
PB6.Signal=I2C1_SCL
PB7.GPIO_Label=Motor_a_fwd
PB7.Signal=GPIO_Output
PB9.Signal=I2C1_SDA
PC13.GPIO_Label=Motor_a_rev
PC13.Signal=GPIO_Output
PC2.GPIO_Label=Motor_b_fwd
PC2.Signal=GPIO_Output
PC3.GPIO_Label=Motor_b_rev
PC3.Signal=GPIO_Output

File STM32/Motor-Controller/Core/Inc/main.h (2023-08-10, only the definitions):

#define Motor_a_rev_Pin GPIO_PIN_13
#define Motor_a_rev_GPIO_Port GPIOC
#define Motor_b_fwd_Pin GPIO_PIN_2
#define Motor_b_fwd_GPIO_Port GPIOC
#define Motor_b_rev_Pin GPIO_PIN_3
#define Motor_b_rev_GPIO_Port GPIOC
#define Motor_a_fwd_Pin GPIO_PIN_7
#define Motor_a_fwd_GPIO_Port GPIOB

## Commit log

2023-04-13 adding kinematic eqs
2023-06-06 3d model construction
    [12V JGY370-D7 DC Gearmotor.step, Assembly.0011.iam, Assembly.iam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]
2023-06-06 3d model finished
    [Assembly.0011.iam, Assembly.0014.iam, Assembly.iam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]
2023-06-06 design notes written
    [Assembly.0014.iam, Assembly.0015.iam, Assembly.iam]
2023-07-14 Starting conversions
    [ANSI (in).dwg, ANSI (in).idw, ANSI (mm).dwg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]
2023-07-14 sdf to use obj
    [robot.sdf]
2023-07-20 Add intertia
    [12x - standoff1.dxf, 1x - back plate.dxf, 1x - front plate.dxf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]
2023-07-20 fix file paths, delete examples
    [robot.sdf]
2023-07-20 revert to 2wheel
    [back_plate.obj, back_plate.stl, body.obj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]
2023-07-20 fix file references
    [back_plate.obj, back_plate.stl, bottom_plate.obj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]
2023-07-21 re add 2wheels
    [body.obj, body.stl, robot.sdf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]
2023-07-21 started flattenning
    [robot.sdf, robot.urdf]
2023-07-23 reconfigured joints
    [ANSI (in).dwg, ANSI (in).idw, ANSI (mm).dwg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]
2023-07-23 update sdf
    [robot.sdf]
2023-07-31 drawing files
    [12x - STANDOFF THICK - 3mm Acrylic.dxf, 12x - standoff1.dxf, 1x - BACK PLATE - 3mm MDF.dxf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]
2023-07-31 build sdf
    [5m_hex_nut.obj, 5m_hex_nut.stl, back_plate.obj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]
2023-08-01 update drawings
    [6mm D SHAFT.0003.idw, 6mm D SHAFT.0004.idw, 6mm D SHAFT.idw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]
2023-08-02 New drawings
    [Assembly.0002.iam, Assembly.0003.iam, Assembly.iam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]
2023-08-02 all drawings
    [3 X 18 HEX HEAD BOLT.0001.idw, 3 X 18 HEX HEAD BOLT.idw, 3 X 6 HEX HEAD BOLT.idw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]
2023-08-03 motor output vector
    [robot.sdf]
2023-08-03 Friction and step climbing
    [frame.obj, frame.stl, robot.sdf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]
2023-08-10 Thursday end
    [4x - SUN GEAR ALTERNATE - 3mm Acrylic.dxf, 8x - IDLER GEAR ALTERNATE - 3mm Acrylic.dxf, 8x - PLANET GEAR ALTERNATE - 3mm Acrylic.dxf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]
2023-08-10 fix gearbox mass
    [frame.obj, frame.stl, robot.sdf]
2023-08-25 import real values
    [robot.sdf, shaft2.obj, shaft2.stl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]
2023-08-25 initial experiment data
    [Experiment.xlsx, Voltage-torque relations.xlsx, masses.xlsx]
2023-08-31 experiment writeup start
    [Experiment.xlsx, Voltage-torque relations.xlsx]
2023-09-09 report writing
    [Experiment.xlsx, Voltage-torque relations.xlsx]
2023-09-15 report writing and solver changes
    [Experiment.xlsx]
2023-09-15 recording current data and validating scale
    [12VNoLoad.csv, 12VStage0.csv, 12VStage1.csv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]
2023-09-19 update solver for inequalities
    [Analysis.xlsx, Experiment.xlsx]
2023-09-22 Calculations: update gear ratio
2023-09-27 add inkscape diagrams
    [Analysis.xlsx, Experiment.xlsx]
2023-10-08 Writeup Expreiment
    [Analysis2.xlsx, Experiment.xlsx, Voltage-torque relations.xlsx]
2023-10-09 more simulation options
    [5m_hex_nut.obj, 5m_hex_nut.stl, back_plate.obj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]
2023-10-20 added find_threshold_torques()
    [5m_hex_nut.obj, 5m_hex_nut.stl, back_plate.obj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]
2023-10-20 more data from model/simulation
    [12x - STANDOFF THICK - 3mm Acrylic.dxf, 24x - STANDOFF THIN - 3mm Acrylic.dxf, 4x - FRAME - 3mm Acrylic.dxf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]
2023-10-21 stage 6 simulation complete
    [Analysis2.xlsx]
2023-10-23 new bigplot
    [New grears.0001.iam, New grears.iam, Spur Gear16.ipt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]
2023-10-24 Inserted friction and gear plots, shortened required torque
2023-10-24 update comparison plots, thicker traces, list of symbols
    [Analysis2.xlsx, Experiment.xlsx]
2023-10-25 model flowchart
2023-10-25 Circuit diagrams, internals, error table
    [Analysis2.xlsx]
2023-10-26 More diagrams
    [Analysis2.xlsx]
2023-10-26 tail and mass plots
    [Analysis2.xlsx, Experiment.xlsx]
2023-10-26 content mostly complete
    [Analysis3.xlsx, Experiment.xlsx, JAW_1_1.stl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]
2023-10-27 report content complete
    [12x - STANDOFF THICK - 3mm Acrylic.dxf, 12x - standoff1.dxf, 1x - BACK PLATE - 3mm MDF.dxf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]
2023-10-27 preparing simulation
    [5m_hex_nut.obj, 5m_hex_nut.stl, back_plate.obj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]
2023-11-07 generating animations for presentation
    [Experiment.xlsx, Voltage-torque relations.xlsx]

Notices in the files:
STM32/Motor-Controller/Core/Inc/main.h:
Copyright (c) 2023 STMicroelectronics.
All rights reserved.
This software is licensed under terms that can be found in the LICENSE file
